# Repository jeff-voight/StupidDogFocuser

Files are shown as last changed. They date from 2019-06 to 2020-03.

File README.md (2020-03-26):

# StupidDogFocuser

## Open-source electronic telescope focuser

The StupidDogFocuser is a work-in-progress prototype electronic focuser. It shall eventually comply with ASCOM and INDI and should operate on Linux, Windows, or Mac.

## Goals

The goal of this project is to develop an electronic focuser that is compact, free of airwires, capable of being mounted to a variety of telescope focusers controllable via a PCB-mounted knob, serial commands, and INDI and ASCOM software. It should be inexpensive, easy to build at home, and only use components that are easy to acquire.

Ultimately, I want somebody to be able to have a neat, compact focuser for under $100 and their time and solder.

## Size and Shape

The PCB is a shield for an Arduino UNO R3. I hope to be able to etch and solder the board at home, but it should also be designed in such a way that one could order a commercially manufactured board. The KiCad design files will be included. The initial builds will be geared toward a commercial board house.

The board is approximately the same shape as the UNO. It receives the 12V power directly from the Arduino. That means that you need to plug the Arduino into a 12V 1A power supply. These are available where you bought the Arduino. We could get more torque and speed if we went with a higher voltage, but we don't really need more torque or speed.

On one end is an optional temperature/humidity sensor. During assembly, the legs of the package need to be bent so that the sensor can be layed flat extended out in space beyond the board. This, hopefully, keeps the sensor far enough away from the driver that it isn't affected and it provides a way to extend the sensor out of an enclosure to give it access to the outdoor air.

The board features a mounted rotary encoder for handheld use. In fact, if one were so inclined, one wouldn't necessarily need to enclose this focuser. One could very easily just put the hat on the arduino, wire up the motor, plug it into 12V, and hold the thing bare and be up and running without an enclosure.

Heck, you could hot glue the whole thing right on your observatory wall or telescope mount and be fine. Maybe clean the spiders out from time to time. I mean, don't let it rain on it, but you weren't going to let it rain on your telescopes, right? 

The encoder has 30 detents, but something I didn't realize at first was that the encoder counts two steps per detent. At first I fretted about this, but at 5400 steps per rotation on a 27:1 geared stepper running at half-stepping (for torque and performance), two steps per detent seemed like an acceptable trade-off. If you're running a 200 step stepper, you *should* still be okay on a refractor or reflector. I can't say for an SCT.

## Enclosure
Included is a 3d-printable set of STL files that worked for me. It even has a knob.

I printed mine in glow-in-the-dark. It has never helped.

I hope to find a more professional enclosure, but I'm not actively looking.

Along with the enclosure, I haven't included the panel-mount electrical connector because I haven't found a 6 pin connector that I like.

I'm currently using a 4-pin aircraft something something. If you have a 6-pin (2 pins for the limit switch) connector that you love and you 
can find it on digikey, feel free to fork the code and submit a pull request.

## Assembly
The PCB is designed to use the same resistors and the same capacitors throughout. You can't go wrong. Just solder the resistors in wherever you see a resistor footprint and the same for the capacitors.

The DHT11 or DHT22 needs to be layed flat if you want it to stick out of an enclosure. This bend needs to be done before soldering.

The motor screw terminals should probably face in the same direction as the wires are going to go. There should be enough space to flip it around.

The Schmidtt Trigger footprint includes a dot and a little slanty line to indicate the dotted end of the chip. Make sure you get the orientation correct.

Likewise, the DRV8825 footprint includes a white rectangle on the same end that the chip of the DRV8825 daughterboard has. Make sure those line up, too.

The DRV8825 *ABSOLUTELY* needs the heatsink that comes with it. Make sure you put that thing on. It didn't take me but a few minutes to roast one of mine during development because I was being lazy.

The DRV8825 *ABSOLUTELY* needs to be adjusted before plugging in your first stepper. The steppers that I've been getting have been running best at about .8A per coil. But, the motor gets HOT.

### DIY disclaimer
I'm not opposed to through-hole parts, but I personally find drilling boards to be the most difficult part of home manufacture of PCB, I'd rather keep the drill-file to a minimum. Consider that you're going to be drilling all of the Arduino header pins and all of the component pins. It's probably safest to order the boards from a board house. However, if you only drill out the holes you need, you can save a whole bunch of the arduino pin holes. You technically only need one ground pin. Make sure you carry the 12V and 5V pins through.

The KiCad PCBs will be done for _my_ convenience for now. That means tiny traces and silkscreen that I wouldn't dare do at home and drill holes galor and if I feel like throwing in a via collection that carries signals and looks like a moose, that's my prerogative.

I mean, I probably won't, but just in case I do.

## Calibration and limit switches

Another goal is a limit switch and a reset routine. Upon hard reset (if there is such a thing), on power-up, it would store it's current position, rack the focuser IN until it touched the limit switch, reset everything such the limit switch is the low limit and the original position gets restored to it's whatever position it was before. I've included the pins for the limit switch, but I haven't yet worked out a homing routine. When it happens, you'll probably need to build a focuser for each telescope you want to drive because the results of the homing and length of focus will get stored in EEPROM.

One way or another, I feel like I need some type of security such that my cameras never fall to the floor or I end up stripping a gear on the focuser.

That said, it hasn't been a problem _yet_.

## Power-Off Conditions

For the time being, all is lost on reset/power-off. We start the focuser in the 20,000s. That should be enough to give a couple of inward turns of a knob.

A limit switch would solve this.

# As it is

As it is, we communicate at 115,200 baud. We depend on AccelStepper and a high performance encoder library, so I don't want to slow either of those down with slow serial performance. Our signal is only going a few feet, and unless you've got outrageous amounts of noise, 115,200 will be fine.

# Commands

Serial commands are as follows:

| Command | Description | Response | Defaults | Comments |
| --- | --- | --- | --- | --- |
| \<HA>	  | Halt | HA! | N/A | as quickly as possible |
| \<GE> 	  | Is enabled? | [T\|F]! | True | Motor Driver |
| \<GR> | Is reversed?| [T\|F]! | False | Motor direction |
| \<GM> | Microsteps  | [1-32]! | _(1/)_1  | Denominator (not yet functional) | 
| \<GH> | High limit  | MAXINT! | 108000 | Distance from initial |
| \<GL> | Low limit | [0! | 0  | 32 bit int |
| \<GS> | Speed | [0-255]! | 255 | Stepper motor dependent |
| \<GT> | Temperature | %f.2! | N/A | DHT11/22 precision  |
| \<GP> | Position | 0-MAXINT! | 0 | Previous focus position |
| \<IM> | Moving? | [T\|F]! | F | True during movement |
| \<AM%d> | Absolute Move | %d! (target) | N/A | Target position|
| \<RM%d> | Relative Move | %d! (target) | N/A | Target position |
| \<RD[T\|F]> | Reverse Motor | [T\|F]! | N/A | Response is new is reversed |
| \<SY%d> | Sync Motor | %d! (same as param) | N/A  | |
| \<EN> | Enable motor | EN! | N/A| ||
| \<DI> | Disable motor| DI! | N/A | |
| \<SM[1-32]> | Set Microstepping 1/1 - 1/32 | %u! | 1 | New microstep mode (not yet functional)|
| \<SP%u> | Set Speed 200-4000 | %d! | New speed | 1000 | Measure your motor to determine |
| \<SH%d> | Set high limit | %d! | 32767 | Response is new high |
| \<SL%d> | Set low limit  | %d! | -32768 | Response is new low limit |

Any error will trigger ERROR(optional message)#

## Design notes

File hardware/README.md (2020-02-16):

The hardware project starts here.

This project includes printed circuit boards (PCB), cases to hold the PCB,
brackets to mount the motor, links to products and datasheets, a BOM to
order a kit, and other whatnot that falls under the category of 'hardware'.

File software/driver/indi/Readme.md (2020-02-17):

# Installation
indi_stupiddogfocuser driver must be compiled in order to use. It does not ship with
the rest of the indi library.

# Features

1. Closed loop focuser
2. Absolute and relative focusing
3. Acceleration built into firmware?
4. Temperature measurement
6. Sync support

# Operation

## Connecting to Stupid Dog Focuser

1. The Stupid Dog Focuser is a built on an Arduino UNO R3, so one connects with a USB A cable.
2. Arduino UNO uses a standard comm/tty port for communication
3. It runs at 9600 baud simply due to the distances involved in a remote observatory.

After connecting, how can you operate the focuser?

## Options

The Options tab contains settings for all drivers that include polling (frequency of updates), logging, and debugging.
 Additional driver-specific options can be added here. If you have any additional settings, list them in detail.

Presets
You may set pre-defined presets for common focuser positions in the Presets tab.

Preset Positions: You may set up to 3 preset positions. When you make a change, the new values will be saved
 in the driver's configuration file and are loaded automatically in subsequent uses.

Preset GOTO: Click any preset to go to that position

Issues
There are no known bugs for this driver. If you found a bug, please report it at https://github.com/jvoight0205/StupidDogFocuser/issues.

http://www.indilib.org/download.html

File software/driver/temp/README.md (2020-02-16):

These files were copied from my first attempt at an ASCOM driver. Preserved here so I can copy/paste code.

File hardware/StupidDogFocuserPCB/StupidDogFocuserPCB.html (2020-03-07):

# C:\Users\jeff\Source\Repos\StupidDogFocuser\hardware\StupidDogFocuserPCB\StupidDogFocuserPCB.sch

3/1/2020 6:51:53 PM

Eeschema (5.1.5)-3

Component Count:17

Ref | Qnty | Value | Part | Datasheet | Description | Vendor
A1 | 1 | Pololu_Breakout_DRV8825 | Driver_Motor:Pololu_Breakout_DRV8825 | https://www.pololu.com/product/2982 | Pololu Breakout Board, Stepper Driver DRV8825
A2 | 1 | Arduino_UNO_R3 | MCU_Module:Arduino_UNO_R3 | https://www.arduino.cc/en/Main/arduinoBoardUno | Arduino UNO Microcontroller Module, release 3
C1, C2, C3, C4, C5 | 5 | 4.7uF | Device:C | ~ | Unpolarized capacitor
M1 | 1 | Stepper_Motor_bipolar | Motor:Stepper_Motor_bipolar | http://www.infineon.com/dgdl/Application-Note-TLE8110EE_driving_UniPolarStepperMotor_V1.1.pdf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 | 4-wire bipolar stepper motor
R1, R2, R3, R4, R5, R6 | 6 | 1k | Device:R | ~ | Resistor
SW1 | 1 | Rotary_Encoder_Switch | Device:Rotary_Encoder_Switch | ~ | Rotary encoder, dual channel, incremental quadrate outputs, with switch
U1 | 1 | DHT11 | Sensor:DHT11 | http://akizukidenshi.com/download/ds/aosong/DHT11.pdf | Temperature and humidity module
U2 | 1 | SN74HC14N | dk_Logic-Gates-and-Inverters:SN74HC14N | http://www.ti.com/general/docs/suppproductinfo.tsp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 | IC INVERTER SCHMITT 6CH 14DIP

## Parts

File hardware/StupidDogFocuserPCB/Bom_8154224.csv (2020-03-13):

Manufacturer Part Number | Manufacturer | Digi-Key Part Number | Customer Reference | Reference Designator | Packaging | Part Status | Quantity | Unit Price | Extended Price | Quantity Available | Mfg Std Lead Time | Description | RoHS Status | Lead Free Status | REACH Status
SN74HC14N | Texas Instruments | 296-1577-5-ND |  |  | Tube | Active | 1 | 0.57000 | $0.57 | 2723 | 12 Weeks | IC INVERTER SCHMITT 6CH 14DIP | ROHS3 Compliant | Lead free | REACH Unaffected
M20-9993646 | Harwin Inc. | 952-1943-ND |  |  | Bulk | Active | 1 | 1.04000 | $1.04 | 420 | 13 Weeks | CONN HEADER VERT 36POS 2.54MM | ROHS3 Compliant | Lead free | REACH Unaffected
PEC12R-4225F-S0024 | Bourns Inc. | PEC12R-4225F-S0024-ND |  |  | Tray | Active | 1 | 1.25000 | $1.25 | 6935 | 16 Weeks | ROTARY ENCODER MECHANICAL 24PPR | ROHS3 Compliant | Lead free | REACH Unaffected
386 | Adafruit Industries LLC | 1528-1228-ND |  |  | Bulk | Active | 1 | 5.00000 | $5.00 | 616 | 2 Weeks | SENSOR HUMID/TEMP 5V DTL 5% MOD | ROHS3 Compliant | Lead free | Not Available
2982 | Pololu Corporation | 2183-2982-ND |  |  | Bulk | Active | 1 | 10.45000 | $10.45 | 148 | Not Available | DRV8825 STEPPER MTR DRVR CARRIER | RoHS Compliant | Not Available | Not Available
OSTTC062162 | On Shore Technology Inc. | ED2613-ND |  |  | Bulk | Active | 1 | 1.29000 | $1.29 | 6285 | 8 Weeks | TERM BLK 6P SIDE ENT 5.08MM PCB | ROHS3 Compliant | Lead free | REACH Unaffected
RNF14FTD54K9 | Stackpole Electronics Inc | RNF14FTD54K9CT-ND |  |  | Cut Tape (CT) | Active | 10 | 0.07200 | $0.72 | 8505 | 20 Weeks | RES 54.9K OHM 1/4W 1% AXIAL | ROHS3 Compliant | Lead free | REACH Unaffected
K223K15X7RF5TH5 | Vishay BC Components | BC1097CT-ND |  |  | Cut Tape (CT) | Active | 10 | 0.15000 | $1.50 | 5840 | 10 Weeks | CAP CER 0.022UF 50V X7R RADIAL | ROHS3 Compliant | Lead free | Not Available

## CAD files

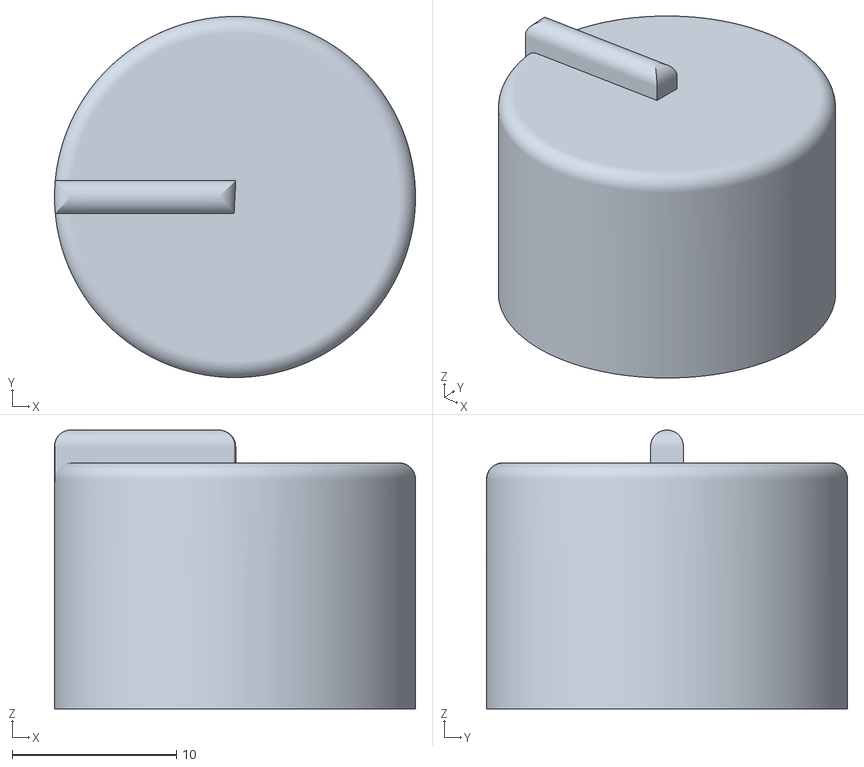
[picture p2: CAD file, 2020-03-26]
hardware/Case/knob.stl
22.0 x 22.0 x 17.0

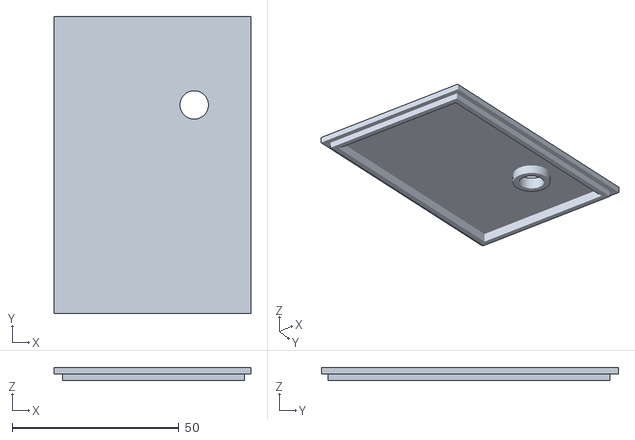
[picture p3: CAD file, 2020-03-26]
hardware/Case/Lid.stl
59.0 x 89.0 x 4.00

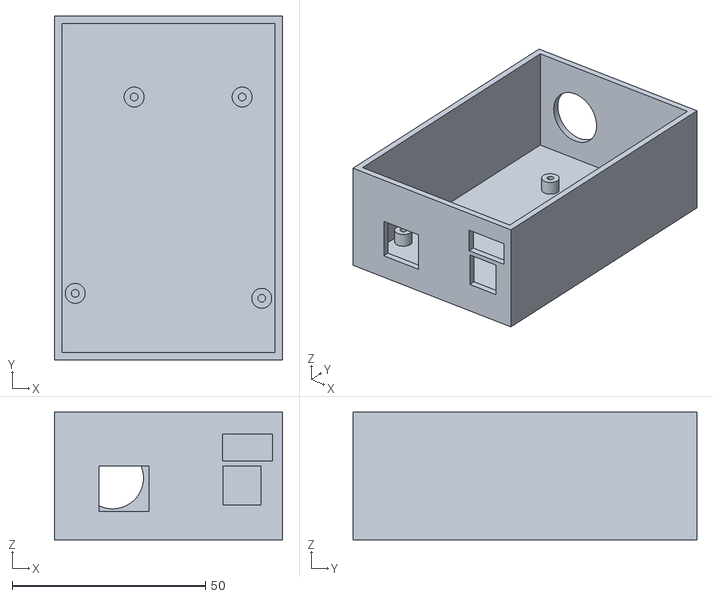
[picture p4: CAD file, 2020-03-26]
hardware/Case/Box.stl
59.0 x 89.0 x 33.0

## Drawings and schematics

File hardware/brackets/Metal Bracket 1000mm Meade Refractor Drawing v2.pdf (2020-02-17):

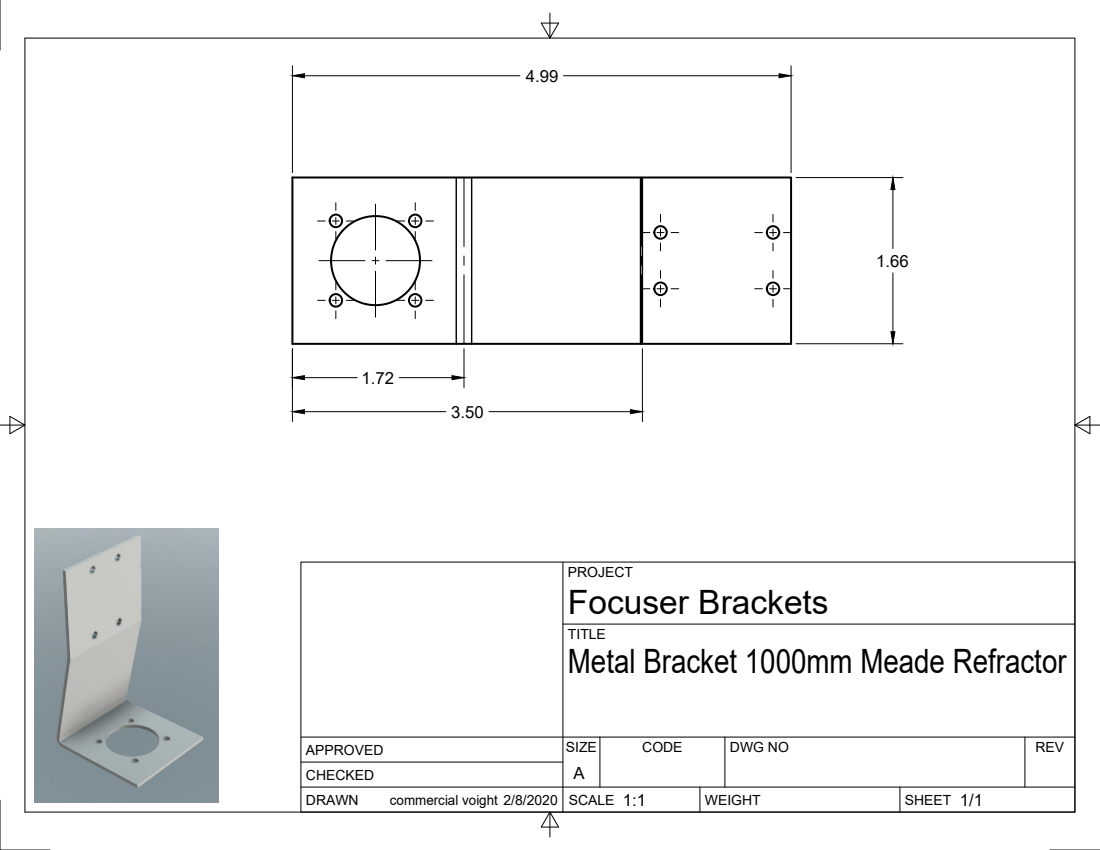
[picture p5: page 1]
SIZE; CODE; DWG NO; REV; commercial voight 2/8/2020

PROJECT
Focuser Brackets
Metal Bracket 1000mm Meade Refractor

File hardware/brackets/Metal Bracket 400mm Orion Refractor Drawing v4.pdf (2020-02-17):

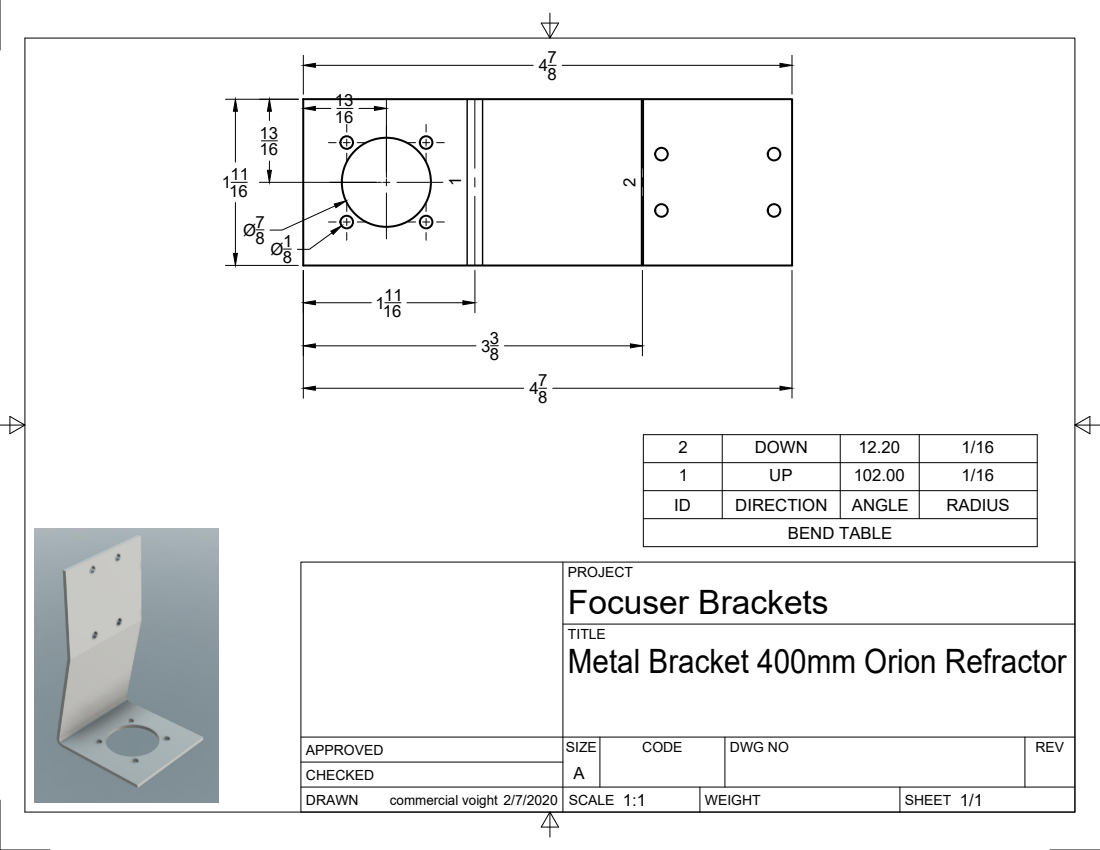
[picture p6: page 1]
SIZE; CODE; DWG NO; REV; commercial voight 2/7/2020; BEND TABLE

2 | DOWN | 12.20 | 1/16
1 | UP | 102.00 | 1/16
ID | DIRECTION | ANGLE | RADIUS

PROJECT
Focuser Brackets
Metal Bracket 400mm Orion Refractor

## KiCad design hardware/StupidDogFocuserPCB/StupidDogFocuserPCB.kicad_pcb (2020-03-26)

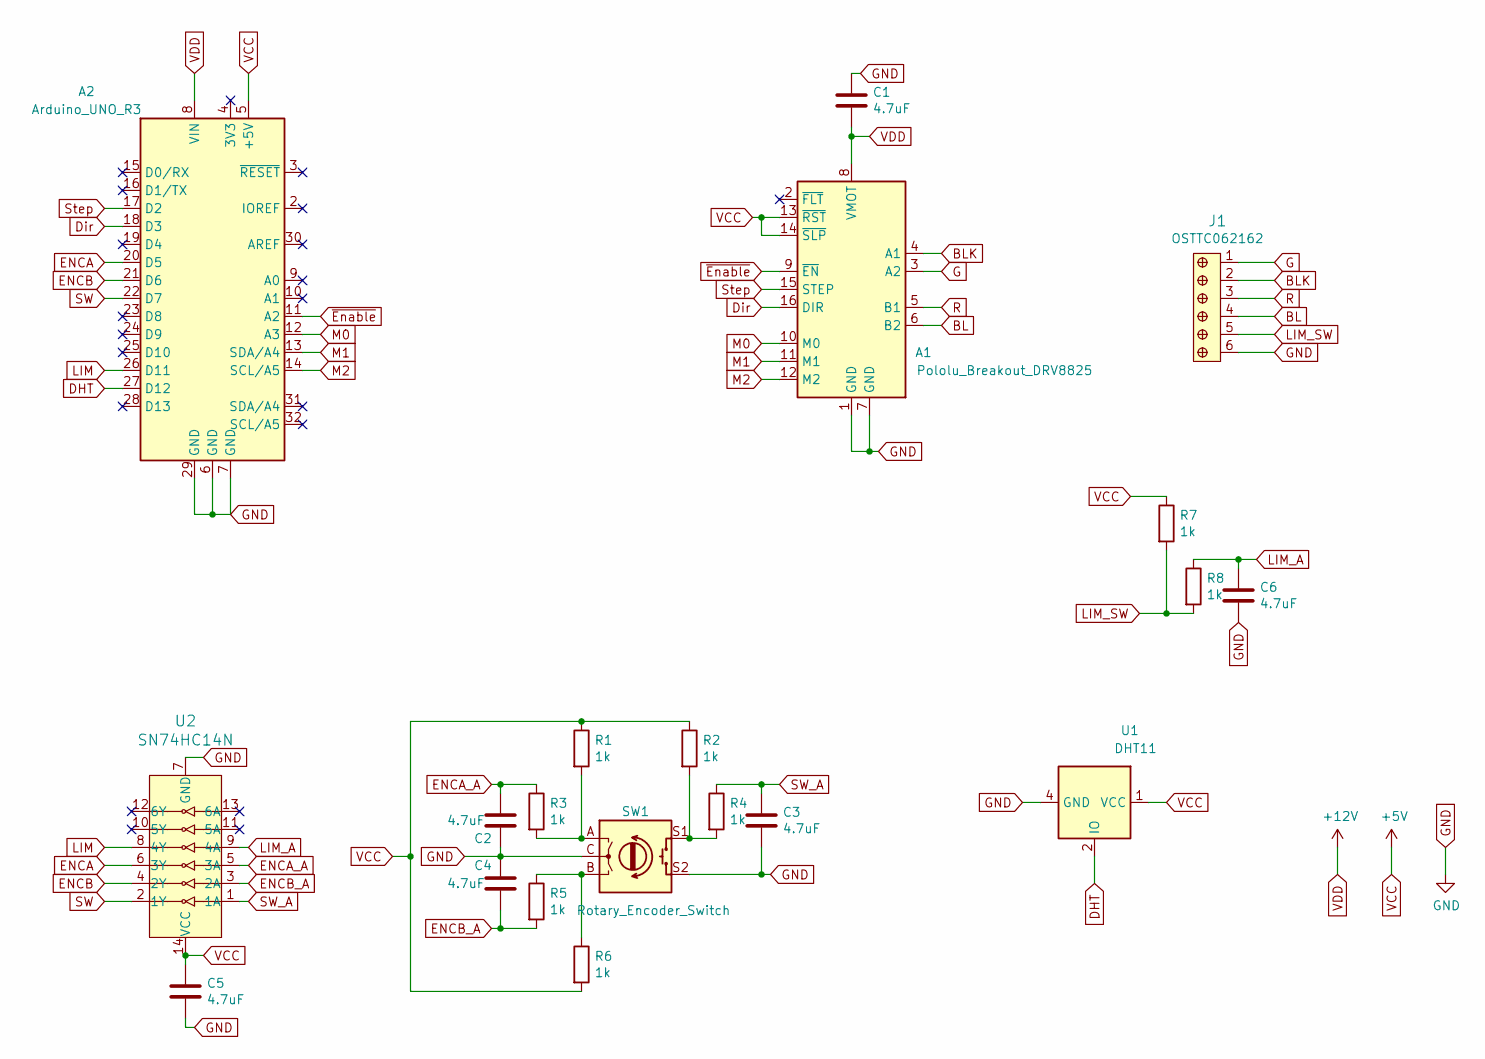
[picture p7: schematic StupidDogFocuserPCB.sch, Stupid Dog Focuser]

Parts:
A1: Pololu_Breakout_DRV8825; Pololu_Breakout-16_15.2x20.3mm
A2: Arduino_UNO_R3
C1, C2, C3, C4, C5, C6: 4.7uF; C_Disc_D4.7mm_W2.5mm_P5.00mm
J1: OSTTC062162; Term_Block_1x6_P5.08mm; MPN OSTTC042162; Digi-Key_PN ED2611-ND
R1, R2, R3, R4, R5, R6, R7, R8: 1k; R_Axial_DIN0204_L3.6mm_D1.6mm_P7.62mm_Horizontal
SW1: Rotary_Encoder_Switch; RotaryEncoder_Alps_EC11E-Switch_Vertical_H20mm
U1: DHT11; Aosong_DHT11_5.5x12.0_P2.54mm
U2: SN74HC14N; DIP-14_W3mm; MPN SN74HC14N; Digi-Key_PN 296-1577-5-ND

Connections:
BL: A1.6 (B2), J1.4
BLK: A1.4 (A1), J1.2
DHT: A2.27 (D12), U1.2 (IO)
Dir: A1.16 (DIR), A2.18 (D3)
ENCA: A2.20 (D5), U2.6 (3Y)
ENCA_A: C2.1, R3.1, U2.5 (3A)
ENCB: A2.21 (D6), U2.4 (2Y)
ENCB_A: C4.2, R5.2, U2.3 (2A)
G: A1.3 (A2), J1.1
GND: A1.1 (GND), A1.7 (GND), A2.6 (GND), A2.7 (GND), A2.29 (GND), C1.1, C2.2, C3.2, C4.1, C5.2, C6.2, J1.6, SW1.C, SW1.S2, U1.4 (GND), U2.7 (GND)
LIM: A2.26 (D11), U2.8 (4Y)
LIM_A: C6.1, R8.1, U2.9 (4A)
LIM_SW: J1.5, R7.2, R8.2
M0: A1.10 (M0), A2.12 (A3)
M1: A1.11 (M1), A2.13 (SDA/A4)
M2: A1.12 (M2), A2.14 (SCL/A5)
unnamed: R1.2, R3.2, SW1.A
unnamed: R2.2, R4.2, SW1.S1
unnamed: R5.1, R6.1, SW1.B
R: A1.5 (B1), J1.3
SW: A2.22 (D7), U2.2 (1Y)
SW_A: C3.1, R4.1, U2.1 (1A)
Step: A1.15 (STEP), A2.17 (D2)
VCC: A1.13 (~RST), A1.14 (~SLP), A2.5 (+5V), C5.1, R1.1, R2.1, R6.2, R7.1, U1.1 (VCC), U2.14 (VCC)
VDD: A1.8 (VMOT), A2.8 (VIN), C1.2
~Enable: A1.9 (~EN), A2.11 (A2)

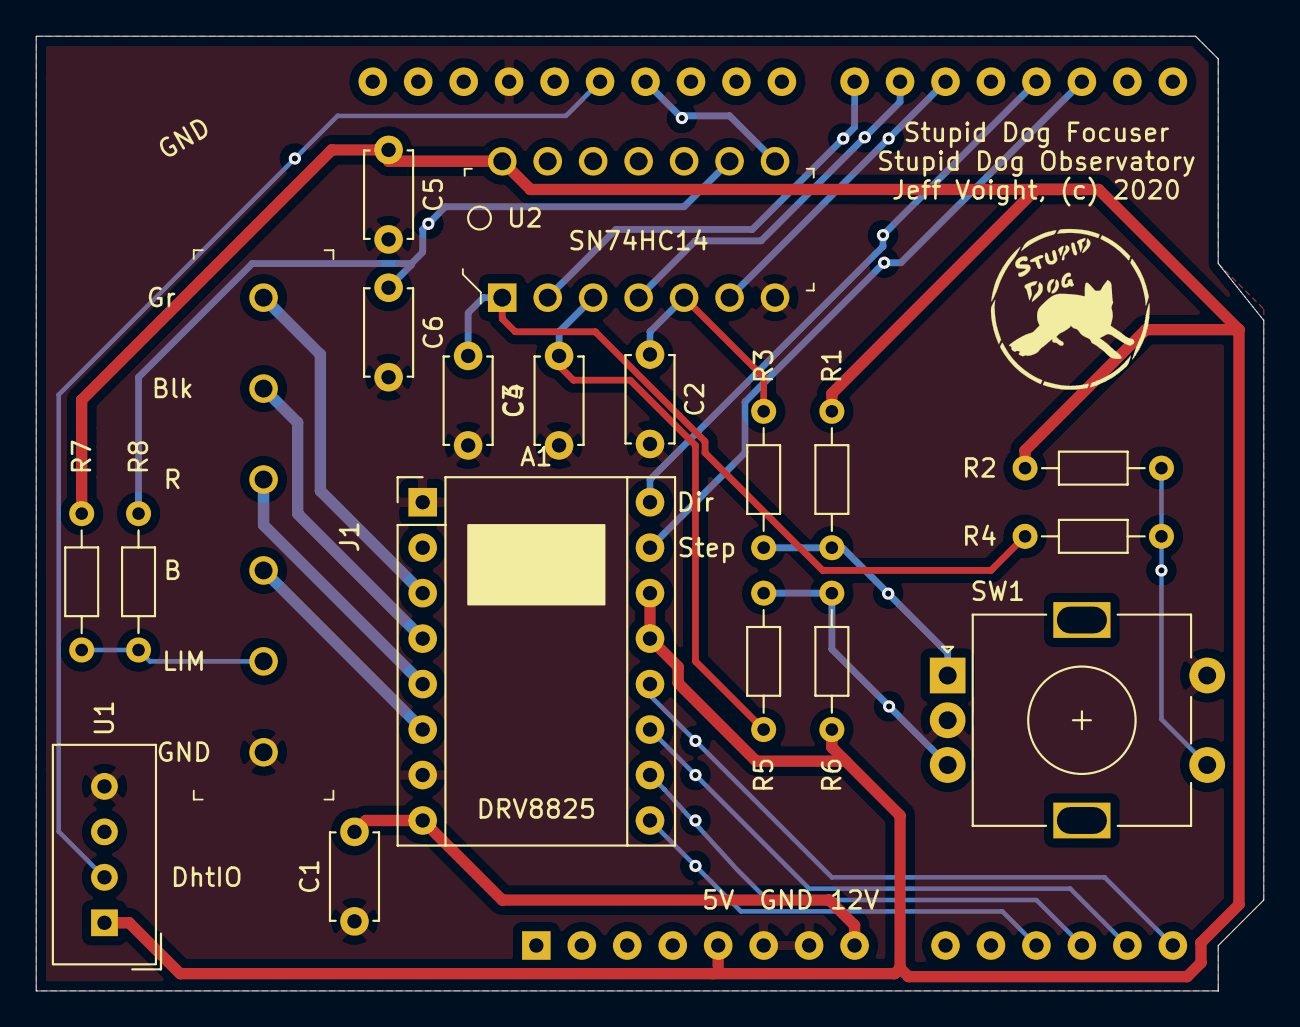
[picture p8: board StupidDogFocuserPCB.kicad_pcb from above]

Board: 2 copper layers, 68.6 x 53.3 mm, 21 parts (1 on the bottom side), 26 nets.

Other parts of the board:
G1: LOGO; Stupid_dog_logo_small

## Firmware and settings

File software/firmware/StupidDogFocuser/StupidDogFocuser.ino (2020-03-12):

#define ENCODER_OPTIMIZE_INTERRUPTS

#include <DHT.h>
#include <Encoder.h>
#include <AccelStepper.h>

/*
    This is the firmware for an Arduino UNO based electronic focuser.
    Stupid Dog Observator
    Written and copyright by Jeff Voight, Feb 2020,

    In order to compile and deploy this, you will need to add the following libraries to your IDE.
      AccelStepper
      Encoder
      DHT Sensor Library


    TODO: Put a normal license here.

    Meanwhile:
    Consider this to be a terribly restrictive license.
    This software contains no warranty of any kind and makes no claims as to it's performance. If it
    erases your favorite photos and murders your friends, it's all on you.
*/

#define STEP_PIN 2
#define DIR_PIN 3
#define ENC_A 5
#define ENC_B 6
#define TURBO_PIN 7
#define LIM_SW 11
#define DHT_PIN 12
#define ENABLE_PIN A2
#define M0_PIN A3
#define M1_PIN A4
#define M2_PIN A5
#define VERSION ".9"
#define TURBO_MULTIPLIER 20


#define DHTTYPE DHT11
//#define DHTTYPE DHT22

// TODO: Figure out how to link this directly to the ASCOM and INDI driver source includes.
#define HALT "HA"
#define IS_ENABLED "GE"
#define IS_REVERSED "GR"
#define GET_MICROSTEP "GM"
#define GET_HIGH_LIMIT "GH"
#define GET_SPEED "GS"
#define GET_TEMPERATURE "GT"
#define GET_POSITION "GP"
#define IS_MOVING "GV"
#define ABSOLUTE_MOVE "AM%ld"
#define RELATIVE_MOVE "RM%ld"
#define REVERSE_DIR "RD"
#define FORWARD_DIR "FD"
#define SYNC_MOTOR "SY%ld"
#define ENABLE_MOTOR "EN"
#define DISABLE_MOTOR "DI"
#define SET_MICROSTEP "SM%u"
#define SET_SPEED "SP%u"
#define SET_HIGH_LIMIT "SH%ld"
#define TRUE_RESPONSE "T"
#define FALSE_RESPONSE "F"
#define SIGNED_RESPONSE "%d"
#define UNSIGNED_RESPONSE "%u"
#define LONG_RESPONSE "%ld"
#define FLOAT_RESPONSE "%f"
#define GET_VERSION "VE"
#define TEMP_DEV -3
#define BUFFER_SIZE 15
// If LIMIT_SWITCH is defined, we'll enable the homing mechanism source code
#define LIMIT_SWITCH

int16_t encoderPosition = 0; // Set to be incorrect on purpose so that it gets updated in setup.
uint32_t startingMotorPosition = 10800; // 10800 is 2 full turns of a 17:1 geared 200 step stepper

// speed needs to map to 255 being the max
/*
 * At 12V, you aren't going to get much better than 1500 steps per second. You can get to 4000
 * if you switch to 1/2 stepping and so on. But, the bottom line is that's probably a bit fast
 * for a focuser that ends up measured in tens of microns. You probably want to keep it below the
 * maximum. Also, keep in mind that every loop needs to potentially interpret a bunch of commands
 * from the driver software. If you're stepping at the max speed, you'll end up missing s55555555555555555555555555555teps
 * if you have to pull a bunch of serial data. Think of 1500 as the very very outside of single-
 * stepping speeds and 3000 for halfstepping. The only time that speed could be important on this
 * is if you have miles to go to reach the limit switch.
 */
uint16_t maxStepperSpeed = 1500; // 1500 for full stepping. 3000 half. 15000 for 1/16th stepping
uint16_t stepperSpeed = maxStepperSpeed; // Gets remapped for INDI
int indiSpeed = 255; // INDI max speed
uint16_t accelRate = 1500; // I've had excellent results with 2000
uint8_t microstep = 2; // can only be multiples of 2
bool enabled = true;
bool reversed = false;

uint32_t highLimit = 108000; // 20 turns of a 17:1, somewhat less for 1/16th microstep
uint32_t targetPosition = 0;
char buffer[BUFFER_SIZE];
char commandLine[BUFFER_SIZE];
bool newData = false;

AccelStepper stepper(AccelStepper::DRIVER, STEP_PIN, DIR_PIN) ; // Skipping enable pin on this
Encoder encoder(ENC_A, ENC_B);
DHT dht(DHT_PIN, DHTTYPE);

void setup() {
  Serial.begin(115200);

  initializeDHT();
  initializeStepper();
  initializeEncoder();

  output(VERSION);
}

void output(String text) {
  Serial.print(text);
  Serial.println("!");
}
/*
   Main loop. We need to call stepper.run() as frequently as possible so the motor doesn't stutter.
   As such, we call stepper.run() between each functional block of code. We don't call it at the very
   end because the loop is just about to be called again and stepper.run() is the first line.

   In this loop, we determine if any serial commands have come in. If so, interpret them. Then we determine
   if any changes have been made to the focus knob. If so, handle them. And, lastly, update the motor
   position variable so that it remains up-to-date at all times.
*/
void loop() {
  stepper.run();

  readSerial();
  stepper.run();

  interpretSerial();
  stepper.run();

  interpretEncoder();
  stepper.run();

}

/**
   Determine if a valid command has been received and act on it.
*/
void interpretSerial() {
  if (newData) {
    long myLong = 0;
    double myDouble = 0.0;

    strcpy(buffer, "              "); // There has to be a better way. I don't know why this doesn't get reset.

    if (strcmp(commandLine, HALT) == 0) {
      stepper.stop();
      while (stepper.isRunning()) { // Call run() as fast as possible to allow motor to halt as quickly as possible
        for (int i = 0; i < 10; i++) { // Can go even faster to halt if we take a bunch of steps between isRunning calls.
          stepper.run();
        }
      }
      long currentPosition = stepper.currentPosition();
      sprintf(buffer, LONG_RESPONSE, currentPosition);
    }

    else if (strcmp(commandLine, IS_ENABLED) == 0) {
      strcpy(buffer, enabled ? TRUE_RESPONSE : FALSE_RESPONSE);
    }

    else if (strcmp(commandLine, IS_REVERSED) == 0) {
      strcpy(buffer, reversed ? REVERSE_DIR : FORWARD_DIR);
    }

    else if (strcmp(commandLine, IS_MOVING) == 0) {
      strcpy(buffer, stepper.isRunning() ? TRUE_RESPONSE : FALSE_RESPONSE);
    }

    else if (strcmp(commandLine, GET_VERSION) == 0) {
      sprintf(buffer, VERSION);
    }

    else if (strcmp(commandLine, GET_MICROSTEP) == 0) {
      sprintf(buffer, UNSIGNED_RESPONSE, microstep);
    }

    else if (strcmp(commandLine, GET_HIGH_LIMIT) == 0) {
      sprintf(buffer, LONG_RESPONSE, highLimit);
    }

    else if (strcmp(commandLine, GET_SPEED) == 0) {
      sprintf(buffer, UNSIGNED_RESPONSE, indiSpeed);
    }

    else if (strcmp(commandLine, GET_TEMPERATURE) == 0) {
      // because of some kind of Arduino bullshit, %f doesn't work the way it's supposed to
      float realTemperature=dht.readTemperature() + TEMP_DEV;
      int8_t intPortion = (int)realTemperature;
      uint8_t floatPortion = abs((int)((realTemperature - intPortion) * 100));
      sprintf(buffer, "%d.%02d", intPortion, floatPortion);
    }

    else if (strcmp(commandLine, GET_POSITION) == 0) {
      long currentPosition = stepper.currentPosition();
      sprintf(buffer, LONG_RESPONSE, currentPosition);
    }

    else if (strcmp(commandLine, ENABLE_MOTOR) == 0) {
      enabled = true;
      stepper.enableOutputs();
      digitalWrite(ENABLE_PIN, LOW);
      strcpy(buffer, enabled ? TRUE_RESPONSE : FALSE_RESPONSE);
    }

    else if (strcmp(commandLine, DISABLE_MOTOR) == 0) {
      enabled = false;
      stepper.disableOutputs();
      digitalWrite(ENABLE_PIN, HIGH);
      strcpy(buffer, enabled ? TRUE_RESPONSE : FALSE_RESPONSE);
    }

    else if (strcmp(commandLine, REVERSE_DIR) == 0) {
      reversed = true;
      strcpy(buffer, reversed ? REVERSE_DIR : FORWARD_DIR);
    }

    else if (strcmp(commandLine, FORWARD_DIR) == 0) {
      reversed = false;
      strcpy(buffer, reversed ? REVERSE_DIR : FORWARD_DIR);
    }

    else if (sscanf(commandLine, SYNC_MOTOR, &myLong) == 1) {
      uint32_t newPosition =  myLong * (reversed ? -1 : 1);
      if (newPosition <= highLimit)
        stepper.setCurrentPosition(myLong);
      sprintf(buffer, LONG_RESPONSE, stepper.currentPosition());
    }

    else if (sscanf(commandLine, ABSOLUTE_MOVE, &myLong) == 1 ) {
      uint32_t newPosition =  myLong * (reversed ? -1 : 1);
      if (newPosition <= highLimit) {
        targetPosition = newPosition;
        stepper.moveTo(targetPosition);
      }
      sprintf(buffer, LONG_RESPONSE, stepper.currentPosition());
    }

    else if (sscanf(commandLine, RELATIVE_MOVE, &myLong) == 1 ) {
      uint32_t newPosition = targetPosition + myLong * (reversed ? -1 : 1);
      if (newPosition <= highLimit) {
        targetPosition = newPosition;
        stepper.moveTo(targetPosition);
      }
      sprintf(buffer, LONG_RESPONSE, stepper.currentPosition());
    }

    else if (sscanf(commandLine, SET_SPEED, &myLong) == 1 ) {
      if (myLong <= 255 ) {
        indiSpeed = myLong;
        stepperSpeed = map(indiSpeed, 1, 255, 1, maxStepperSpeed);
        stepper.setMaxSpeed(stepperSpeed);
      }
      sprintf(buffer, UNSIGNED_RESPONSE, indiSpeed);
    }

    else if (sscanf(commandLine, SET_MICROSTEP, &myLong) == 1 ) {
      setMicrostep((int)myLong);
      sprintf(buffer, UNSIGNED_RESPONSE, microstep);
    }

    else if (sscanf(commandLine, SET_HIGH_LIMIT, &myLong) == 1 ) {
      if (myLong <= 999999999)
        highLimit = myLong;
      sprintf(buffer, LONG_RESPONSE, highLimit);
    }
   
    output(buffer);
    newData = false;
  }
}


void readSerial() {
  static boolean recvInProgress = false;
  static byte ndx = 0;
  char startMarker = '<';
  char endMarker = '>';
  char rc;

  while (Serial.available() > 0 && !newData) {
    rc = Serial.read();

    if (recvInProgress) { // If we're already receiving, append
      if (rc != endMarker) { // Make sure it isn't the end marker
        commandLine[ndx] = rc;
        ndx++;
        if (ndx >= BUFFER_SIZE) {
          ndx = BUFFER_SIZE - 1; // keeps the buffer from overflowing
        }
      } else {                   // If it is the end marker
        commandLine[ndx] = '\0'; // terminate the string
        recvInProgress = false;  // We're no longer receiving
        ndx = 0;
        newData = true;         // TADA
      }
    }

    else if (rc == startMarker) { // Look for the start marker
      recvInProgress = true;
    }
  }
}

/*
   Determine if the encoder has moved this cycle. If so, make the adjustments
   to the stepper and update variables.
*/
void interpretEncoder() {
  long newEncoderPosition = encoder.read();
  if (newEncoderPosition != encoderPosition) {                  // If there's any change from the previous read,
    long encoderChange = (newEncoderPosition - encoderPosition) * getTurboMultiplier();  // determine the difference and multiply it by current turbo
    stepper.moveTo(stepper.targetPosition() + encoderChange);  // set the new target
  }
  encoderPosition = newEncoderPosition;                       // reset the encoder status
}

/*
   Read the turbo button and apply a multiplier if necessary
*/
uint16_t getTurboMultiplier() {
  return digitalRead(TURBO_PIN) == HIGH ? TURBO_MULTIPLIER : 1;
}

/*
   Initialize the stepper motor.
*/
void initializeStepper() {
  stepper.setMaxSpeed(map(indiSpeed, 1, 255, 1, maxStepperSpeed));
  stepper.setAcceleration(accelRate);
  stepper.setCurrentPosition(startingMotorPosition);
  pinMode(ENABLE_PIN, OUTPUT);
  digitalWrite(ENABLE_PIN, LOW);
  pinMode(M0_PIN, OUTPUT);
  pinMode(M1_PIN, OUTPUT);
  pinMode(M2_PIN, OUTPUT);
  setMicrostep(microstep);
  // TODO: Homing sequence
}

void setMicrostep(int ms) {
  uint8_t m0 = LOW, m1 = LOW, m2 = LOW;
  switch (ms) {
    case 1:
      microstep = 1;
      break;
    case 2:
      microstep = 2;
      m0 = HIGH;
      break;
    case 4:
      microstep = 4;
      m1 = HIGH;
      break;
    case 8:
      microstep = 8;
      m0 = HIGH; m1 = HIGH;
      break;
    case 16:
      microstep = 16;
      m2 = HIGH;
      break;
    case 32:
      microstep = 32;
      m0 = HIGH; m2 = HIGH;
      break;
    default:
      break;
  }
  // TODO: Speed multiplier when microstepped because the motor can handle the speeds when it microsteps.
  digitalWrite(M0_PIN, m0);
  digitalWrite(M1_PIN, m1);
  digitalWrite(M2_PIN, m2);
}
/*
   Initialize the encoder. For now, just the turbo button
*/
void initializeEncoder() {
  pinMode(TURBO_PIN, INPUT);
}

/*
   Initialize the temperature sensor
*/
void initializeDHT() {
  pinMode(DHT_PIN, INPUT_PULLUP);
  dht.begin();
}

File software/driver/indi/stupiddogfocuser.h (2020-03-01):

/*
    Stupid Dog Focuser
    Stupid Dog Observatory
    Copyright 2020 Jeff Voight (jeff.voight@gmail.com)

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
 */

#pragma once

#include "indifocuser.h"
#include "connectionplugins/connectionserial.h"

#define HALT "HA"
#define IS_ENABLED "GE"
#define IS_REVERSED "GR"
#define GET_MICROSTEP "GM"
#define GET_HIGH_LIMIT "GH"
#define GET_SPEED "GS"
#define GET_TEMPERATURE "GT"
#define GET_POSITION "GP"
#define IS_MOVING "GV"
#define ABSOLUTE_MOVE "AM%ld"
#define RELATIVE_MOVE "RM%ld"
#define REVERSE_DIR "RD"
#define FORWARD_DIR "FD"
#define SYNC_MOTOR "SY%ld"
#define ENABLE_MOTOR "EN"
#define DISABLE_MOTOR "DI"
#define SET_MICROSTEP "SM%u"
#define SET_SPEED "SP%u"
#define SET_HIGH_LIMIT "SH%ld"
#define TRUE_RESPONSE "T"
#define FALSE_RESPONSE "F"
#define SIGNED_RESPONSE "%d"
#define UNSIGNED_RESPONSE "%u"
#define LONG_RESPONSE "%ld"
#define FLOAT_RESPONSE "%f"
#define GET_VERSION "VE"


// Version should match hardware response to make sure our protocol works.
#define VERSION ".9"

#define MAX_BUFFER 64

class StupidDogFocuser : public INDI::Focuser {
public:
    StupidDogFocuser();
    virtual ~StupidDogFocuser() override = default;

    typedef enum {
        M1, M2, M4, M8, M16, M32
    } MicrostepMode;


    virtual bool ISNewNumber(const char *dev, const char *name, double values[], char *names[], int n) override;
    virtual bool ISNewSwitch(const char *dev, const char *name, ISState *states, char *names[], int n) override;
    bool SetFocuserMicrostep(int _microstep);

protected:
    virtual bool Handshake() override;
    const char *getDefaultName() override;
    virtual bool initProperties() override;
    virtual bool updateProperties() override;
    virtual IPState MoveAbsFocuser(uint32_t targetTicks) override;
    virtual IPState MoveRelFocuser(FocusDirection dir, uint32_t ticks) override;
    virtual bool AbortFocuser() override;
    virtual bool SyncFocuser(uint32_t ticks) override;
    virtual bool SetFocuserSpeed(int speed) override;
    virtual void TimerHit() override;



private:
    int sendCommand(char *cmd, char *res);
    void GetFocusParams();
    int readFocuserPosition();
    int readFocuserTemperature();
    int readFocuserSpeed();
    int readFocuserMicrostep();
    int readFocuserFirmware(char *_focuser_cmd, char *_focuser_reply);
    int sendFocuserPositionAbsolute(uint32_t newTarget);
    int sendFocuserSyncPosition(const double *newPosition);
    int sendFocuserSpeed(int *speed);
    int sendFocuserMicrostep(int *microstep);
    int readFocuserMoving();
    int sendFocuserEnable();
    int sendFocuserDisable();
    int sendFocuserHighLimit(double *highLimit);



    int timerID{ -1};
    double targetPos{ 0};
    bool simulatedMoving{false};
    int8_t dir{1};
    uint8_t microstep{1};
    uint8_t speed{255};
    double simulatedTemperature{ 0};
    double simulatedPosition{ 0};
    char commandBuffer[MAX_BUFFER];
    char responseBuffer[MAX_BUFFER];

    ILight MovingL[1];
    ILightVectorProperty MovingLP;

    INumber TemperatureN[1];
    INumberVectorProperty TemperatureNP;

    // Step mode
    ISwitch MicrostepModeS[6];
    ISwitchVectorProperty MicrostepModeSP;

    ISwitch Enabled[2];
    ISwitchVectorProperty EnabledSP;

    // Update status and perform maintenance every 2 seconds 

    // Time for the arduino to boot up.
    static const uint8_t ML_TIMEOUT{ 5};
};

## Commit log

2020-02-17 brackets (#11)
2020-02-17 kicad drawing. Single layer. I don't like it. (#12)
    [StupidDogFocuserPCB.kicad_pcb, StupidDogFocuserPCB.sch]
2020-02-17 Remap/pins (#14)
    * Remapped kicad pins. Still need to map firmware.
    * no connections added to unused pins.
    * moved dht pin.
    * moved pins in sketch. Added optimize interrupts flag. Changed error messages.
    [StupidDogFocuserPCB.kicad_pcb, StupidDogFocuserPCB.sch]
2020-02-19 Indi/clearout (#16)
    * gitignore
    * Deleted Backlash, speed controls, and switches.
    * Serial Connection. Updated sendCommand and readResponse to handle tty.
    * erant trace removed
    * thicker traces
    * gitignore
    * Deleted Backlash, speed controls, and switches.
    * Serial Connection. Updated sendCommand and readResponse to handle tty.
    * erant trace removed
    * thicker traces
    [StupidDogFocuserPCB.kicad_pcb]
2020-02-24 Hardware/cleanup (#22)
    * added m1 and m2
    * gerbers
    [StupidDogFocuserPCB-B_Cu.gbr, StupidDogFocuserPCB-B_Mask.gbr, StupidDogFocuserPCB-B_Paste.gbr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]
2020-03-01 Command refactor (#23)
    * checkpoint
    * got the indi driver working sort of
    * serial working for now.
    * checkpoint
    * got the indi driver working sort of
    * serial working for now.
    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
2020-03-07 Hardware/bugs (#26)
    * ASCOM6 Template
    * ASCOM commands ported in from firmware
    * remove readme.htm. Will replace with Readme.md when I get around to it.
    * Updated schematic. Added limit switch. Moved encoder to the right and the stepper to the left. Adjusted resistor and capacitor sizes. Added screw terminals. Moved DHT11 to where it can bend out.
    * thicker traces for the home gamer. Cleanup bends. Moved test points around.
    * regenerate gerbers
    * pcb
    [StupidDogFocuserPCB-B_Cu.gbr, StupidDogFocuserPCB-B_Mask.gbr, StupidDogFocuserPCB-B_Paste.gbr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]
2020-03-07 Firmware/pinupdate (#27)
    * iml file ignored
    * Change pin definitions. Did some light housekeeping.
2020-03-12 Feature/pcbready (#30)
    * cache update kicad?
    * added temperature read back in
    * minor tweaks to the code now that the PCB works.
    * update indi driver to reflect changes. Remove microstep.
    * speed read
    [StupidDogFocuserPCB.sch]
2020-03-13 Feature/bompcbpads (#31)
    * bill of materials
    * added ground clip pad. Updated capacitor sizes. Regenerated gerbers.
    [Bom_8154224.csv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]
2020-03-13 Feature/ascom driver (#34)
    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
2020-03-26 Feature/case st ls (#35)
    * larger holes for screw terminals. Ground pad for testing.
    * Updating Readme
    [Box.stl, Lid.stl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]

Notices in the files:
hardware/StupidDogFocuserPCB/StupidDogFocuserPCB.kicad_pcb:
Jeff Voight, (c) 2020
